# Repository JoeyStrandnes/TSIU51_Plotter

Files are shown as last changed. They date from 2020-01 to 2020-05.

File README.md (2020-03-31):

# Skittle Sort



Skittle sort är en sorteringsmaskin för kursen "Mikrodatorprojektet".

- 2x Servomotorer
- 2x ATMega16A
- 3D printad trumma 
- jm162a 2x16 numerisk LCD
- TCS34725 (RGB sensor)

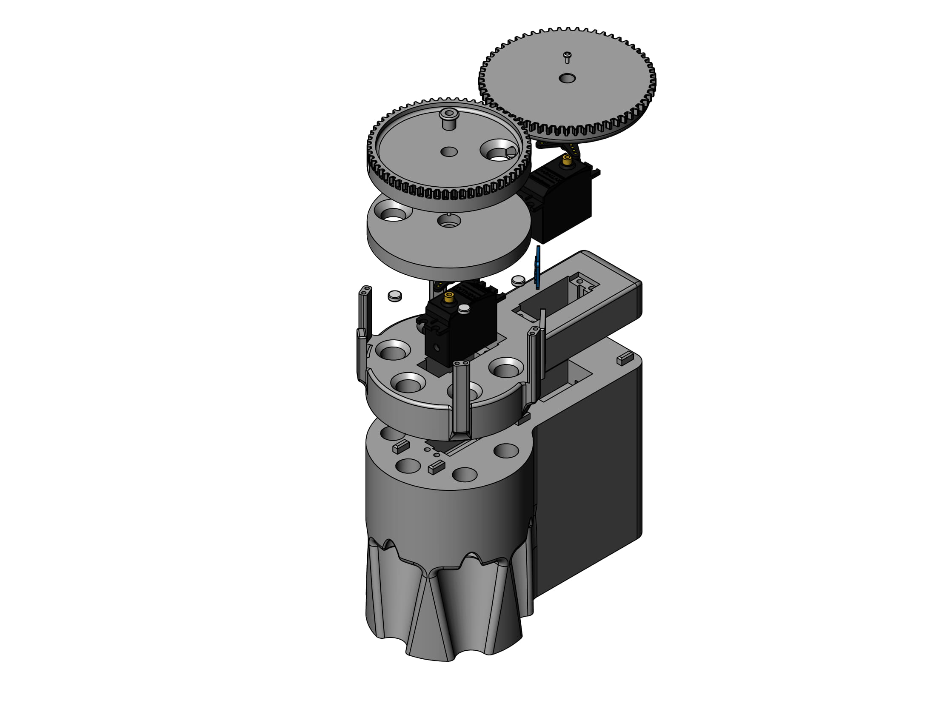
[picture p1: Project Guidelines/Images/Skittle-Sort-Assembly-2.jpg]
Assembly


PCB
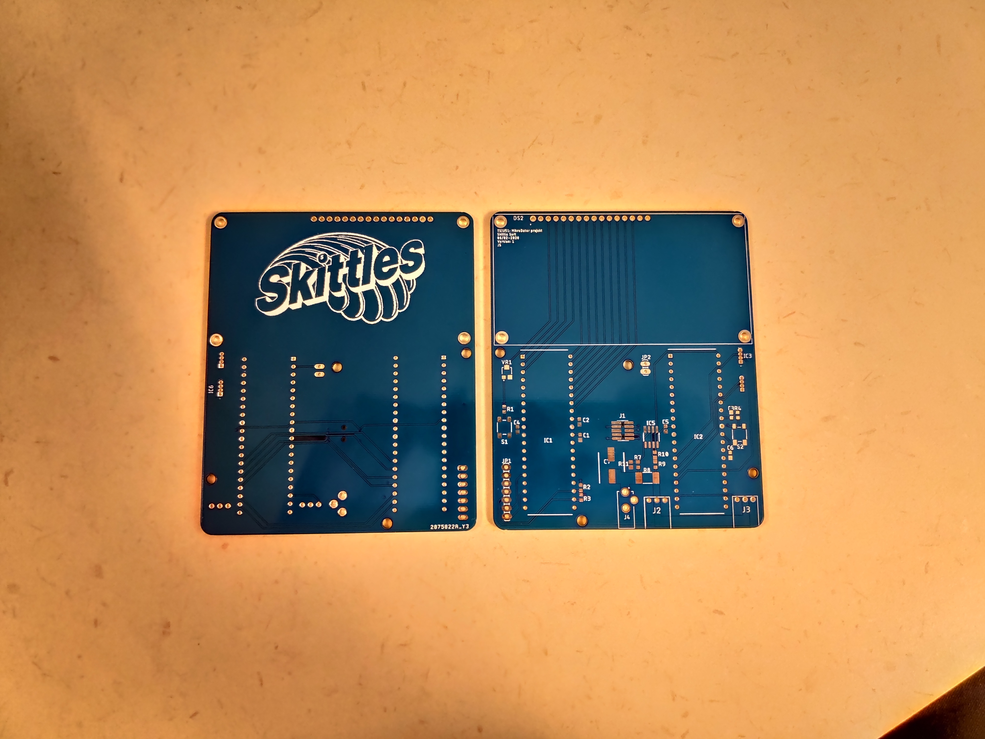
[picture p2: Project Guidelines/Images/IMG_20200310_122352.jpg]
PCB


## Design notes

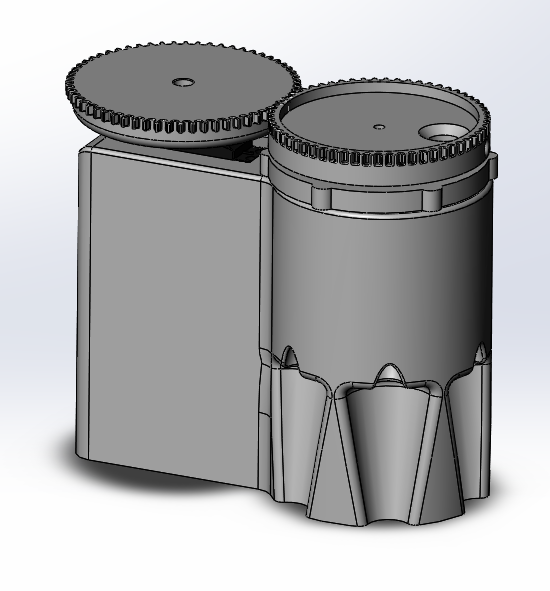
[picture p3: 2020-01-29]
Mechanical/Images/More Complete-2.png

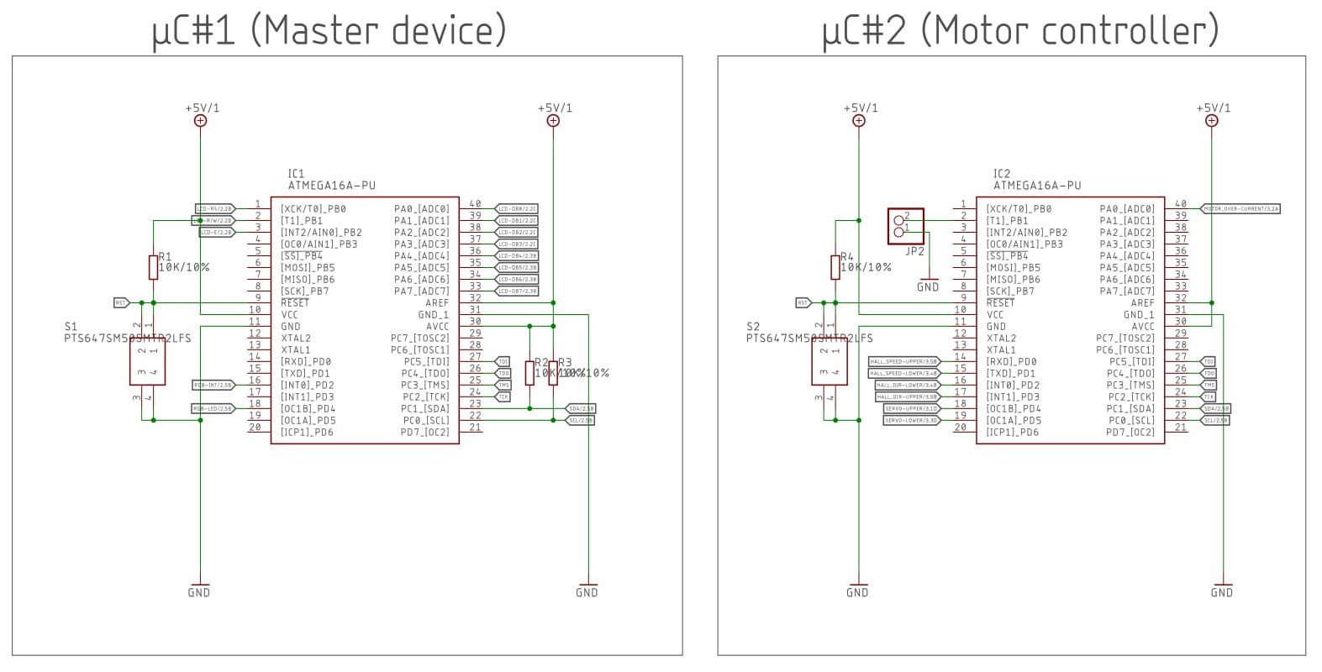
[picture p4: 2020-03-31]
Project Guidelines/Images/Schematic/Microcontroller.jpg

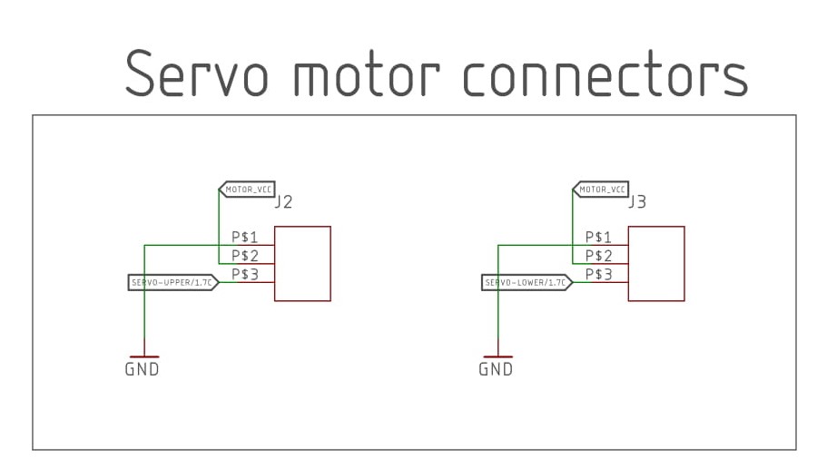
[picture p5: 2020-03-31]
Project Guidelines/Images/Schematic/Servo.jpg

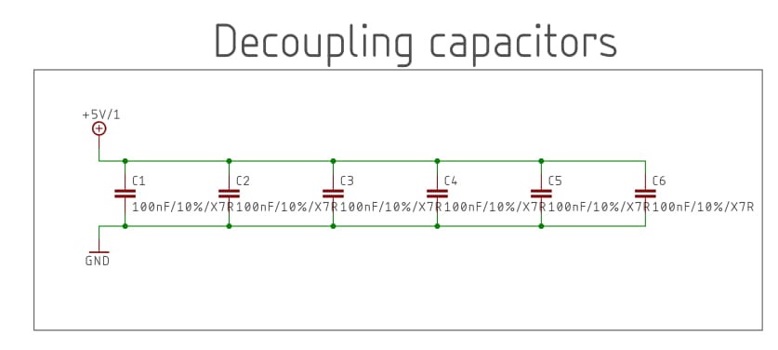
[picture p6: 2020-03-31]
Project Guidelines/Images/Schematic/Decoupling.jpg

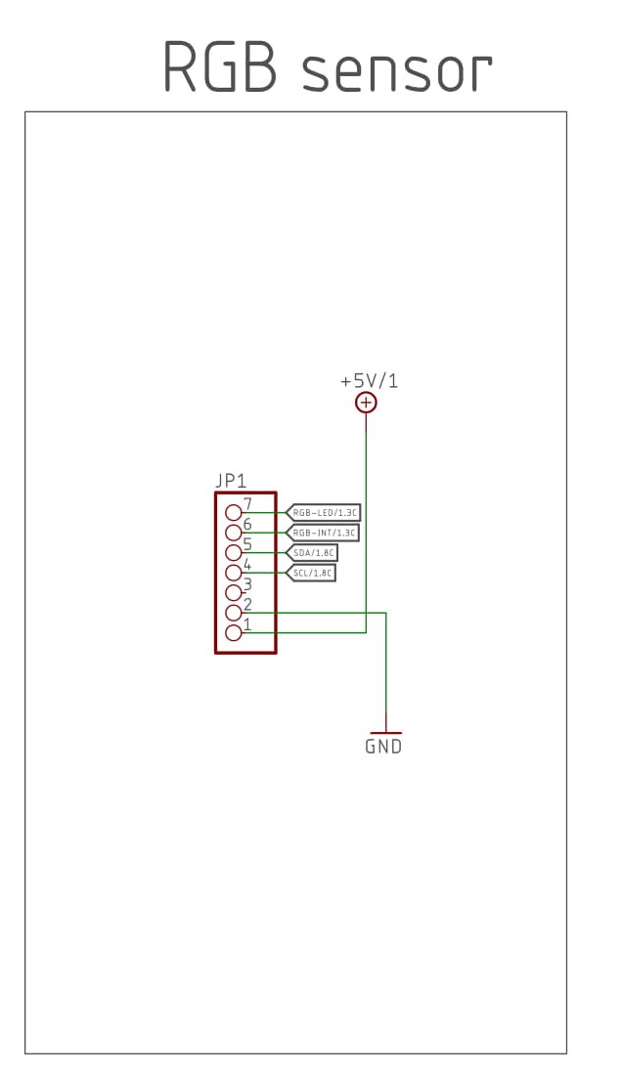
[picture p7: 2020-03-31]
Project Guidelines/Images/Schematic/RGB.jpg

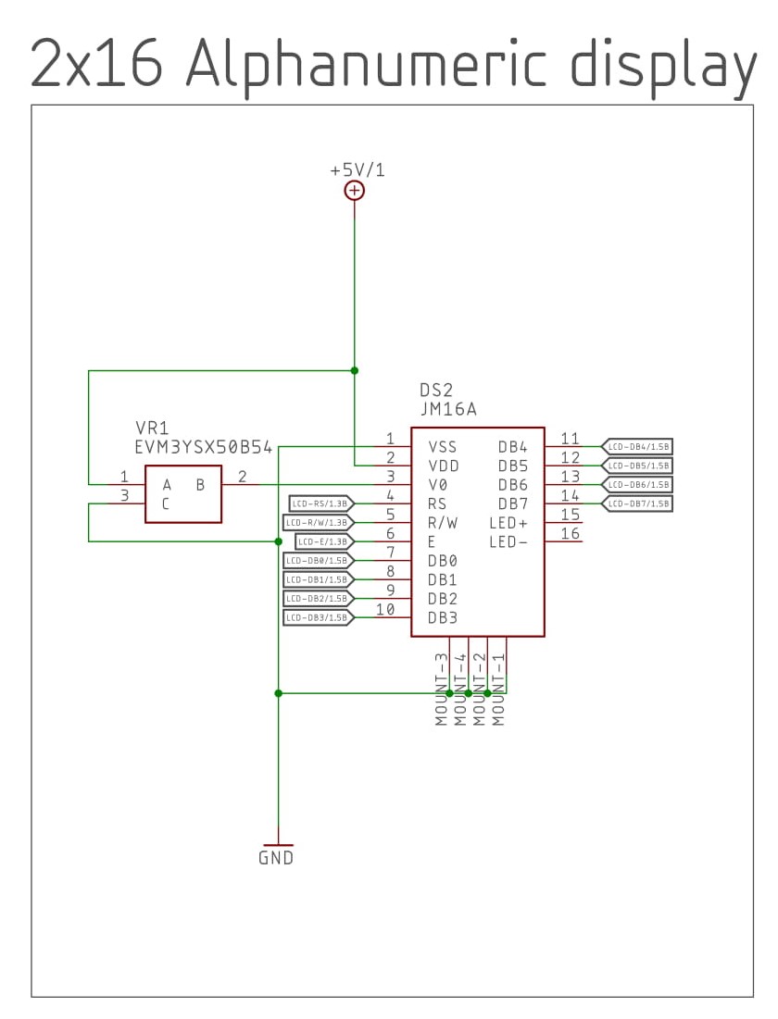
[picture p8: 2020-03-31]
Project Guidelines/Images/Schematic/LCD.jpg

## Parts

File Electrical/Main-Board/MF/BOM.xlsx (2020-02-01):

Qty | Value | Device | Package | Description | Purchase Link
2 | 22288033 | 22288033 | 22288033 | Pin header | https://se.rs-online.com/web/p/pcb-headers/1790561/
5 | 1.2K/5% | R-EU_R0603 | R0603 | RESISTOR, European symbol | https://se.rs-online.com/web/p/surface-mount-fixed-resistors/6621026/
6 | 100nF/10%/X7R | C-EUC0603 | C0603 | CAPACITOR, European symbol | https://se.rs-online.com/web/p/mlccs-multilayer-ceramic-capacitors/9040240/
6 | 10K/10% | R-EU_R0603 | R0603 | RESISTOR, European symbol | https://se.rs-online.com/web/p/surface-mount-fixed-resistors/8626704/
1 | 200R/5% | R-EU_R0603 | R0603 | RESISTOR, European symbol | https://se.rs-online.com/web/p/surface-mount-fixed-resistors/6789960/
2 | 500R/5% | R-EU_R0603 | R0603 | RESISTOR, European symbol | https://se.rs-online.com/web/p/surface-mount-fixed-resistors/1228894/
1 | 866R/5% | R-EU_R0603 | R0603 | RESISTOR, European symbol | https://se.rs-online.com/web/p/surface-mount-fixed-resistors/1229654/
2 | ATMEGA16A-PU | ATMEGA16A-PU | DIP1556W56P254L5232H483Q40N | ATMEGA16A-PU, 8 bit AVR Microcontroller 16MHz 16 kB, OBS: INGET MÅSTE, DRAR BARA NER STORLEKEN | https://se.rs-online.com/web/p/microcontrollers/1278276/
1 | AZ1117CH-5.0TRG1DITR-ND | AZ1117CH-5.0TRG1DITR-ND | SOT230P700X180-4N | LOW DROPOUT LINEAR REGULATOR | https://se.rs-online.com/web/p/low-dropout-voltage-regulators/9210688/
1 | AZ1117CH-ADJTRG1 | AZ1117CH-ADJTRG1 | SOT230P700X170-4N | 1.35A Adj. LDO Reg. Current Limit SOT223 DiodesZetex | https://se.rs-online.com/web/p/low-dropout-voltage-regulators/8287602/
1 | EEEFK1J220P | EEEFK1J220P | CAPAE800X650N | Panasonic Aluminium Electrolytic Capacitor 22uF 63V | https://se.rs-online.com/web/p/aluminium-capacitors/7083598/
1 | ERJ-L1WKF10CU | ERJ-L1WKF10CU | RESC6332X120N | RESISTOR, 2512 100 mOhm +/-1% 1W | https://se.rs-online.com/web/p/surface-mount-fixed-resistors/0566989/
1 | EVM3YSX50B54 | EVM3YSX50B54 | EVM3YSX50B54 | SMD Cermet Trimmer Pot, 3mm Sq, 50K | https://se.rs-online.com/web/p/trimmer-resistors/7312880/
1 | FTSH-105-01-L-DV-K-A-P-TR | FTSH-105-01-L-DV-K-A-P-TR | FTSH10501LDVKAPTR | Samtec FTSH, 1.27mm Pitch, 10 Way, 2 Row PCB Termina | https://se.rs-online.com/web/p/pcb-headers/0451732/
1 | LM2904DRG3 | LM2904DRG3 | SOIC127P600X175-8N | Dual general-purpose operational amplifier (Finns ej på RS, nästa bästa) | https://se.rs-online.com/web/p/op-amps/1449253/
1 | NHD-0216XZ-FSW-GBW | NHD-0216XZ-FSW-GBW | NHD0216XZFSWGBW | LCD Character Display Modules & Accessories STN- GRA | -
1 | PJ-031DH | PJ-031DH | PJ031DH | DC Power Connectors Power Jacks (Finns ej på RS, nästa bästa) | https://se.rs-online.com/web/p/dc-power-sockets/1224871/
2 | PTS647SM50SMTR2LFS | PTS647SM50SMTR2LFS | PTS647SM50SMTR2LFS | Tactile Switches 50mA 12VDC, 1.8N 5.0mm H, G leads (Finns ej på RS, nästa bästa) | https://se.rs-online.com/web/p/tactile-switches/0255667/
5 | TLE4966L | TLE4966L | TLE4966L | Infineon TLE4966L, Bipolar Hall Effect Sensor Switch | https://se.rs-online.com/web/p/hall-effect-sensor-ics/1107464/
2 | Servo Motor |  |  |  | https://se.rs-online.com/web/p/servo-motors/7813046/

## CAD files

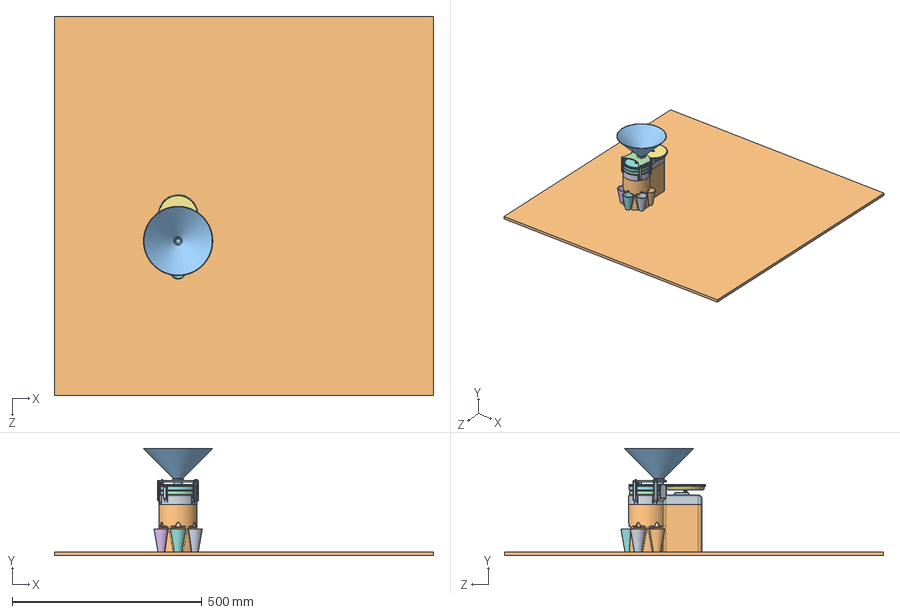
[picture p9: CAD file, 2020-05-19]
Mechanical/Skittle-Sort-Assembly.SLDASM
1000.0 x 283.4 x 1000.0 mm
Slide-Top
User Library-Futaba-Parallax-ContinuousRatationServo x 2
Lower-Disk
User Library-Futaba-Servo-X-Horn x 2
2mm-Screw x 2
Upper-Servo-Gear
Upper-Disk-ALT
Shaft-Spacer
Slide-Bottom
tcs34725
Upper-Shaft-Retainer
Magnet-8mm x 5
Glass-R
Glass-G
Glass-Y
Glass-O
Glass-P
M3x16mm x 2
Transistor_TO-92_Type

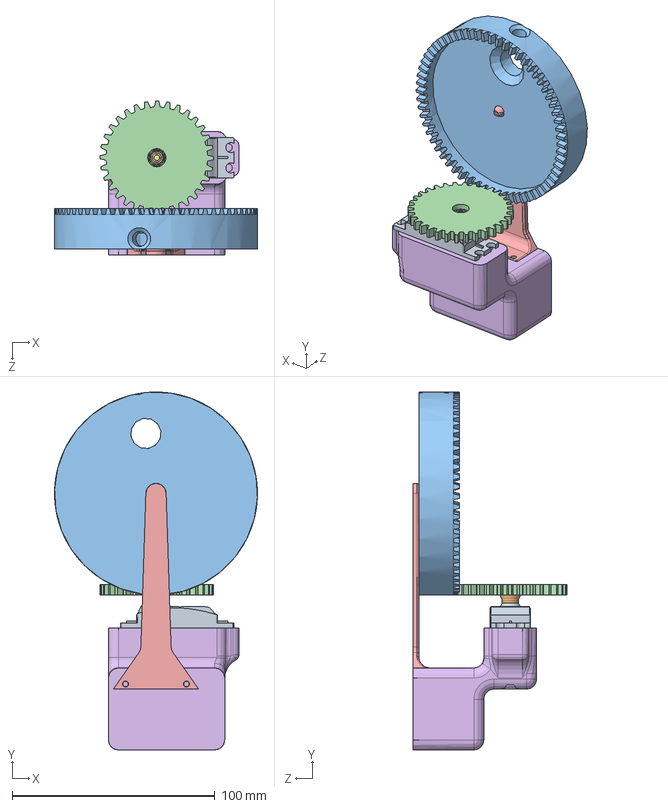
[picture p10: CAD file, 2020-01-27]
Mechanical/Top-Sorter-SubAssembly.SLDASM
100.0 x 176.4 x 76.0 mm
User Library-Futaba-Parallax-ContinuousRatationServo
User Library-Futaba-Servo-X-Horn
Upper-Disk
Upper-Servo-Gear
Top-Holder
Top-Motor-Holder
2mm-Screw

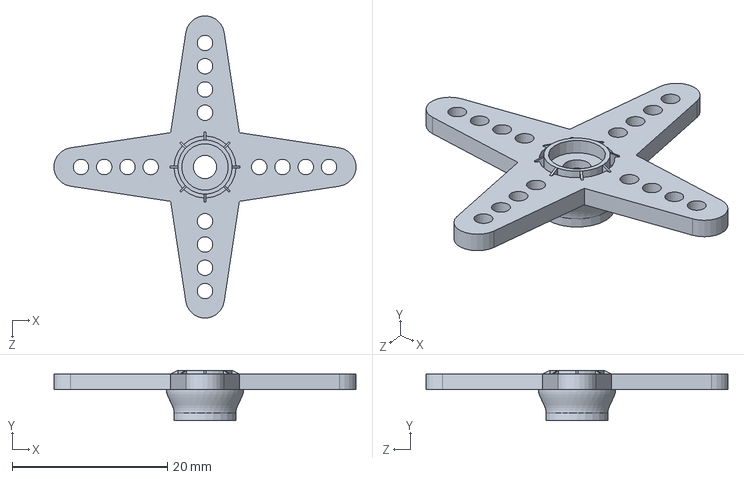
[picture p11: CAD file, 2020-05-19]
Mechanical/Servo From manufacturer/User Library-Futaba-Servo-X-Horn.sldprt
39.0 x 6.50 x 39.0 mm

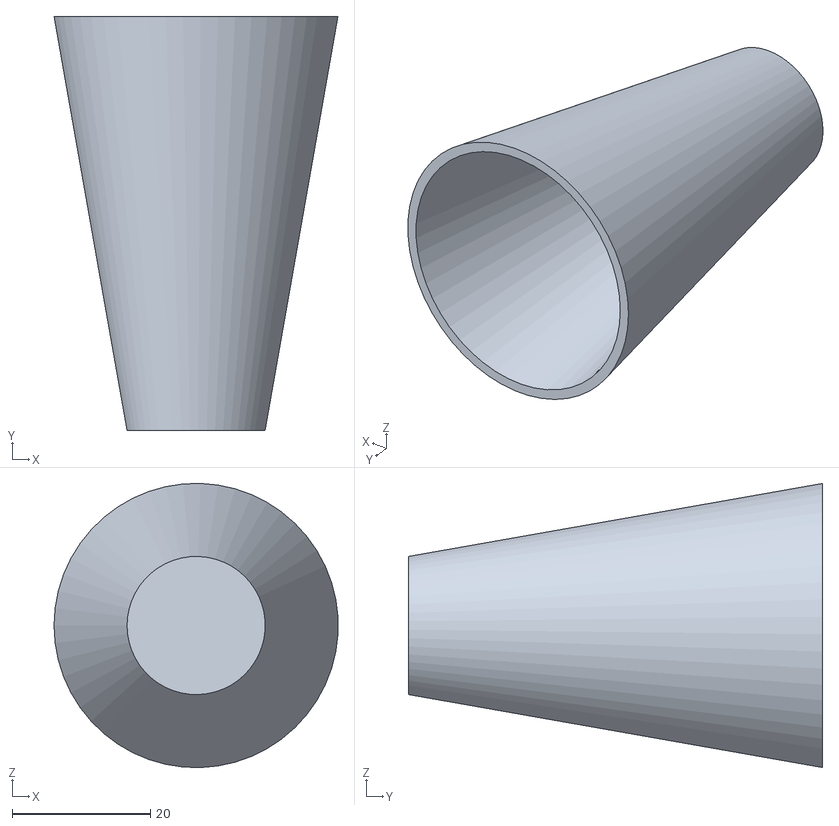
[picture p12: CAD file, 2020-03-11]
Mechanical/STL Files/Cup.STL
41.1 x 60.0 x 41.1

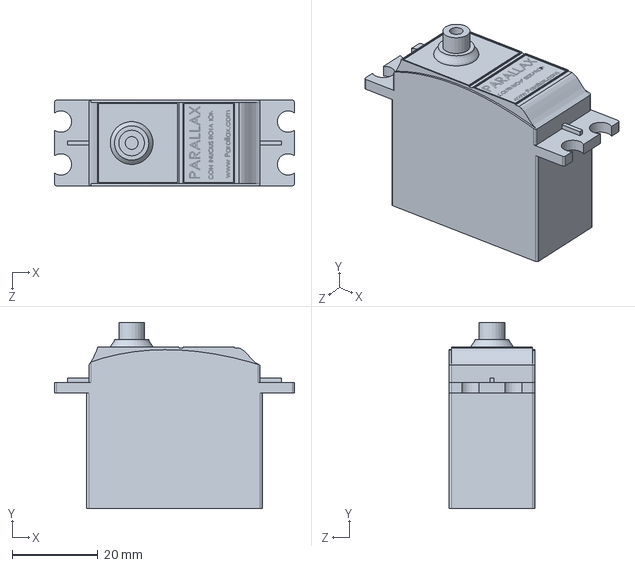
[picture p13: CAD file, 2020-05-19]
Mechanical/Servo From manufacturer/User Library-Futaba-Parallax-ContinuousRatationServo.sldprt
56.0 x 43.5 x 20.0 mm

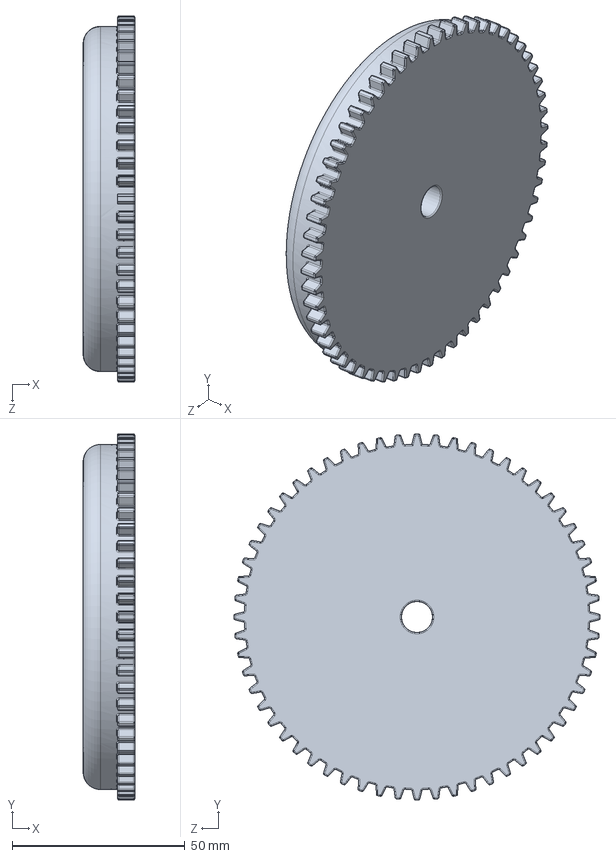
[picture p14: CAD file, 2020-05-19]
Mechanical/Upper-Servo-Gear.SLDPRT
15.0 x 106.0 x 106.0 mm

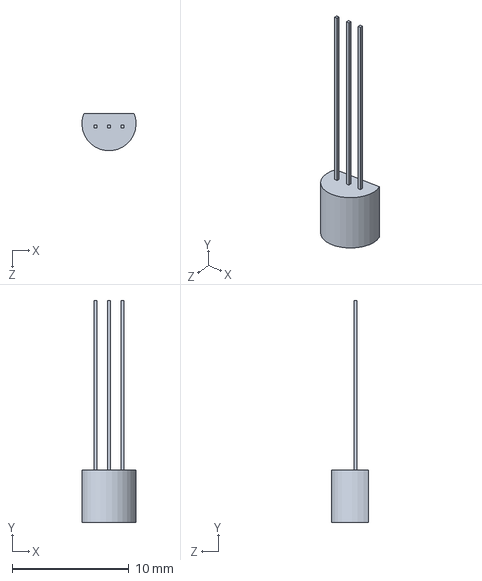
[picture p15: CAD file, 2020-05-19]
Mechanical/Transistor_TO-92_Type.SLDPRT
4.64 x 19.0 x 3.19 mm

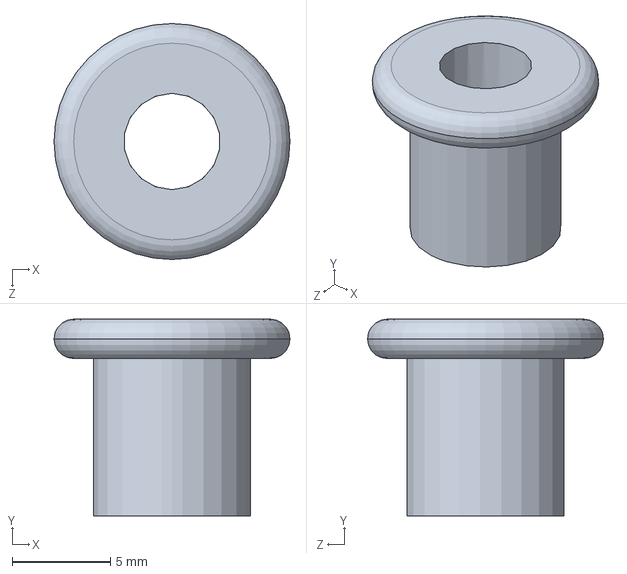
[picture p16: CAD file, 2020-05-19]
Mechanical/Upper-Shaft-Retainer.SLDPRT
12.0 x 10.0 x 12.0 mm

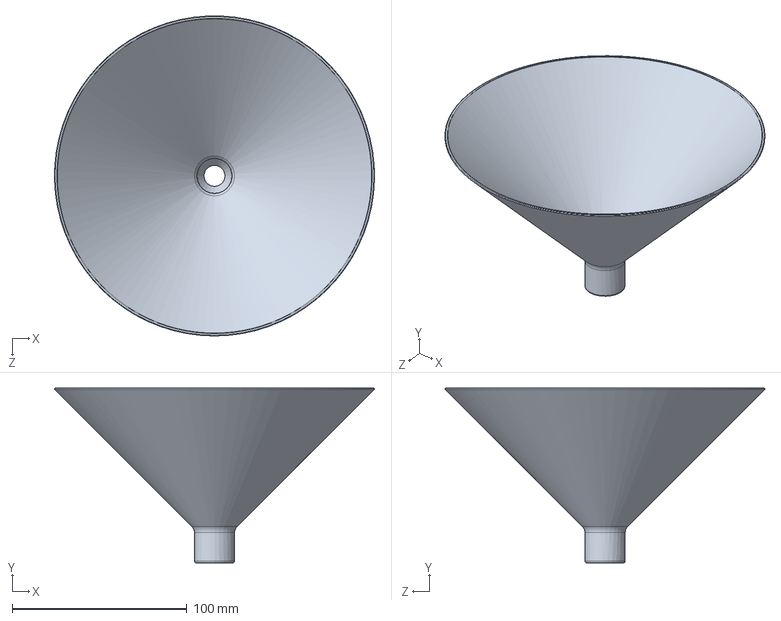
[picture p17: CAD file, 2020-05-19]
Mechanical/Funnel.SLDPRT
183.1 x 100.0 x 183.0 mm

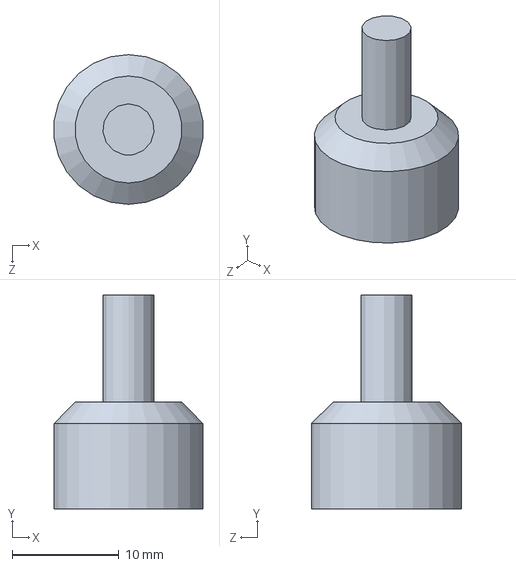
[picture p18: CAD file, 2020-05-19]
Mechanical/Shaft-Spacer.SLDPRT
13.9 x 20.0 x 14.0 mm

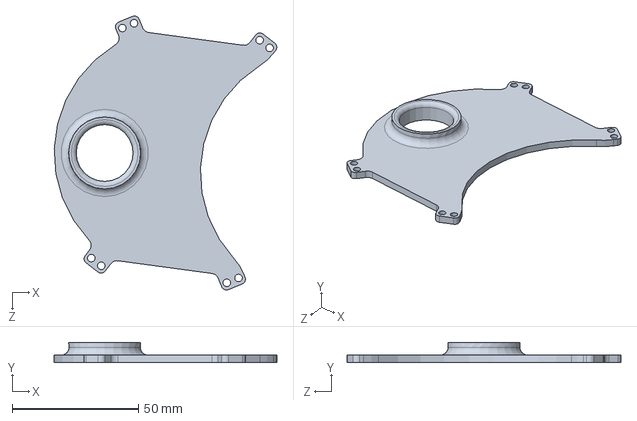
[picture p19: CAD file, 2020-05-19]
Mechanical/Funnel Retainer.SLDPRT
88.1 x 8.00 x 108.5 mm

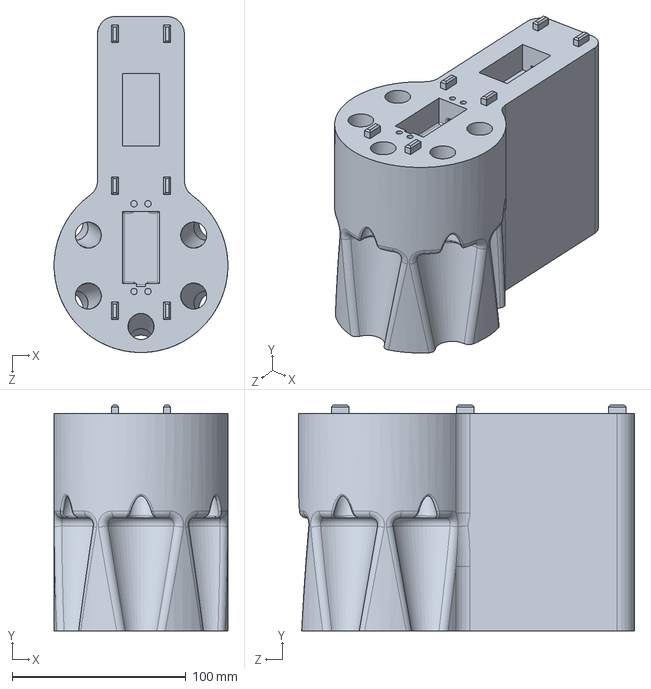
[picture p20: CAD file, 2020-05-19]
Mechanical/Slide-Bottom.SLDPRT
100.0 x 130.0 x 193.3 mm

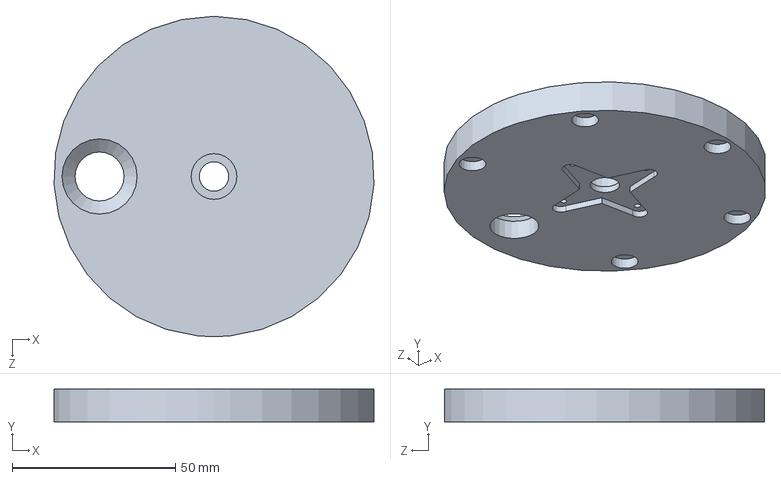
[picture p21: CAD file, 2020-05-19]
Mechanical/Lower-Disk.SLDPRT
97.9 x 10.0 x 98.0 mm

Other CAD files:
Mechanical/Glass-G.SLDPRT
Mechanical/Glass-P.SLDPRT
Mechanical/Glass-R.SLDPRT
Mechanical/Glass-O.SLDPRT
Mechanical/Glass-Y.SLDPRT
Mechanical/2mm-Screw.SLDPRT
Mechanical/Drawings/Disk-Draw.SLDDRW
Mechanical/Floor.SLDPRT
Mechanical/Glass.SLDPRT
Mechanical/M3x16mm.SLDPRT
Mechanical/Magnet-8mm.SLDPRT
Mechanical/Parallax-900-000XX_ServoMotor.SLDPRT
Mechanical/STL Files/Funnel Retainer.STL
Mechanical/STL Files/Funnel.STL
Mechanical/STL Files/Lower-Disk.STL
Mechanical/STL Files/Slide-Bottom.STL
Mechanical/STL Files/Slide-Top.STL
Mechanical/STL Files/Upper-Shaft-Retainer.STL
Mechanical/Skittle.SLDPRT
Mechanical/Slide-BACKUP.SLDPRT
Mechanical/Slide-Top.SLDPRT
Mechanical/Top-Holder.SLDPRT
Mechanical/Top-Motor-Holder.SLDPRT
Mechanical/Upper-Disk-ALT.SLDPRT
Mechanical/Upper-Disk-Retainer.SLDPRT
Mechanical/Upper-Disk.SLDPRT
Mechanical/tcs34725.sldprt

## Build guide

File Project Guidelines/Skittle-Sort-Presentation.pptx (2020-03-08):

## Skittle Sort

Mikrodatorprojekt - TSIU51

## Krav & Mål

- Sortera Skittles beroende på färg
- Visa data på LCD
- Kommunicera över I2C

## Funktionsdiagram

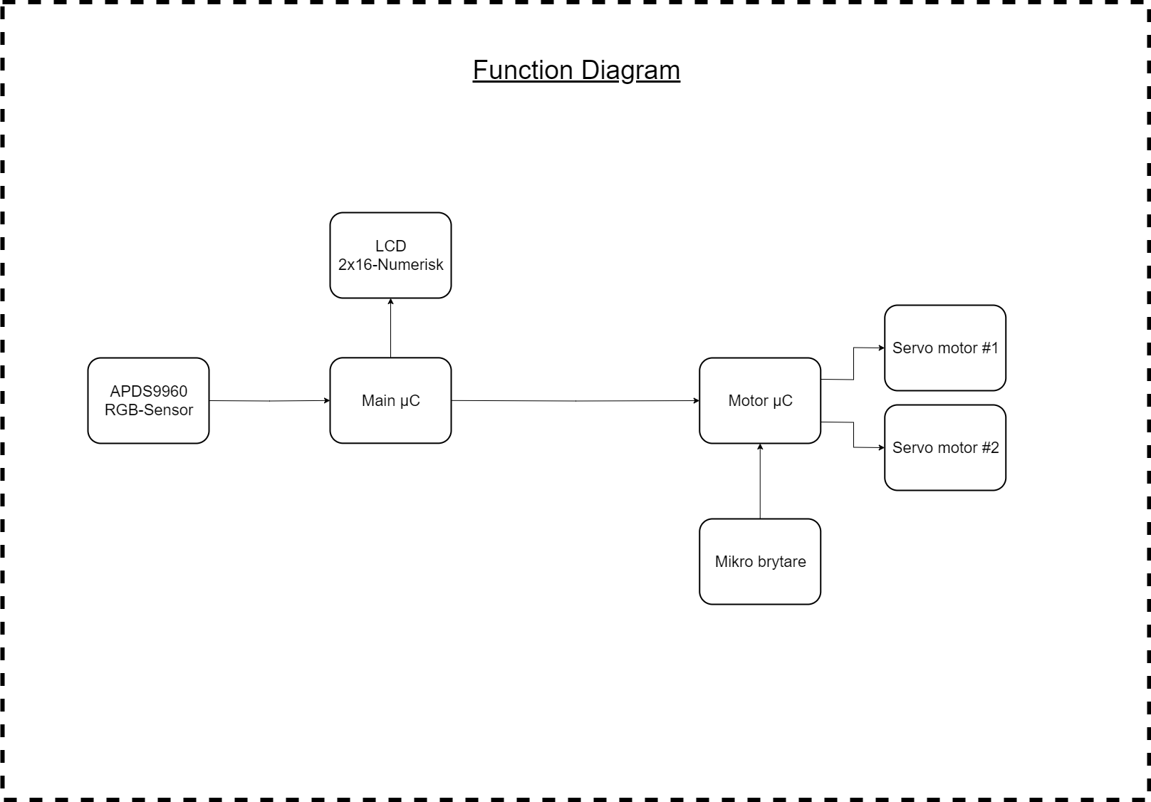
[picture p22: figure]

## Elektronik

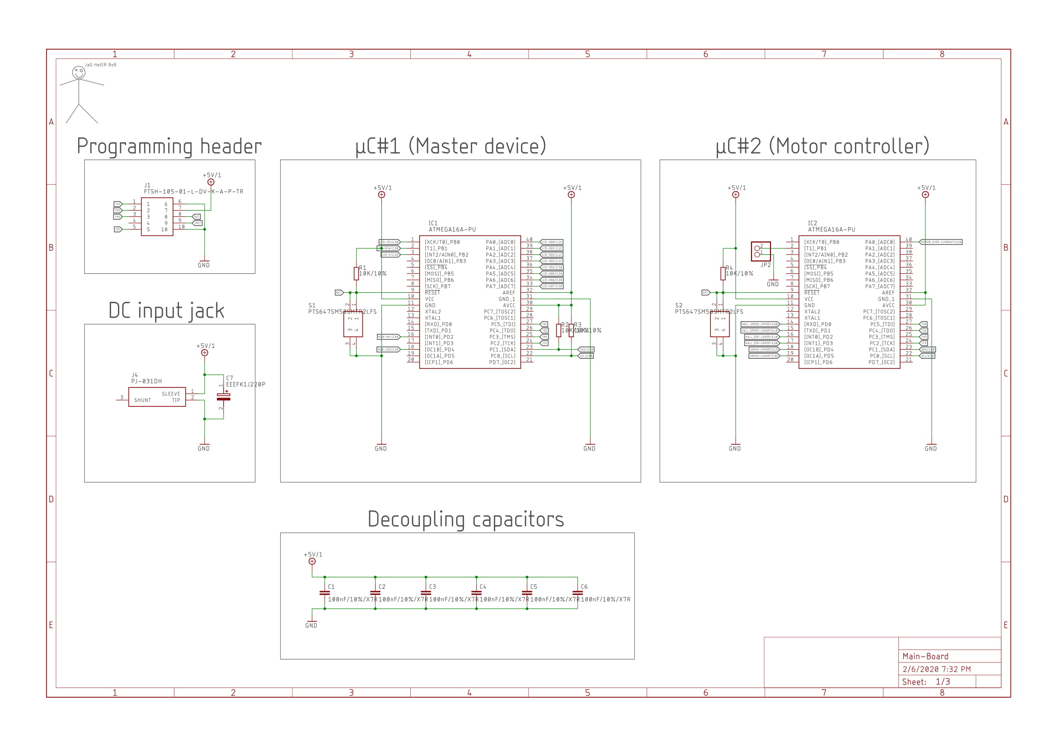
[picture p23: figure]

JM16A (LCD)
TCS34725 (RGB sensor)
LM2904DRG3
2x ATMega16A
2x A1120/22
2x Parallax 900-00008

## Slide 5

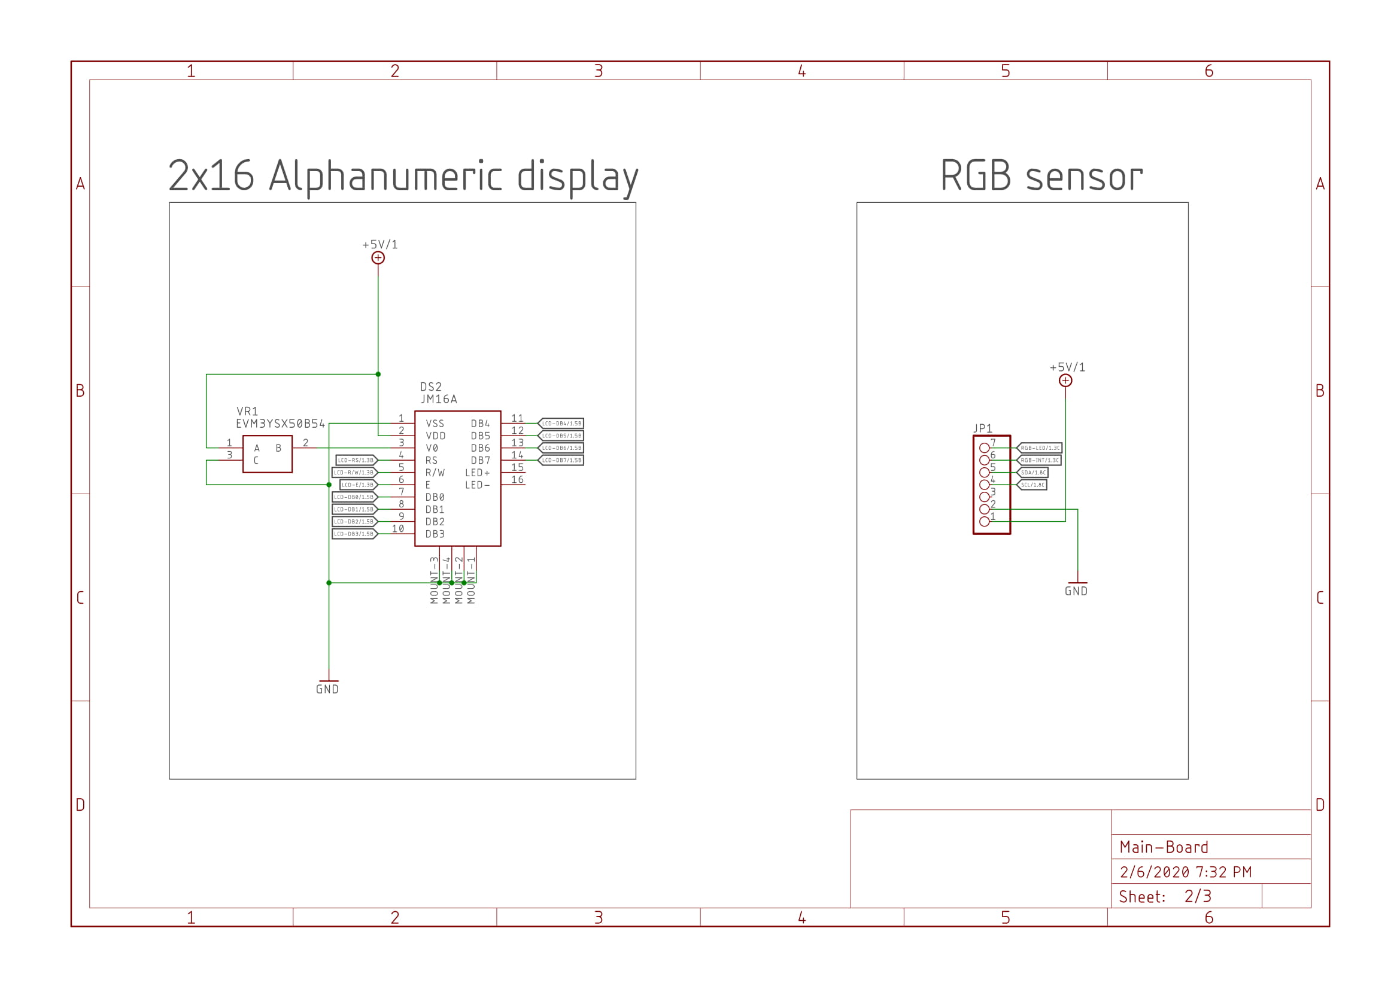
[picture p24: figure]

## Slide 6

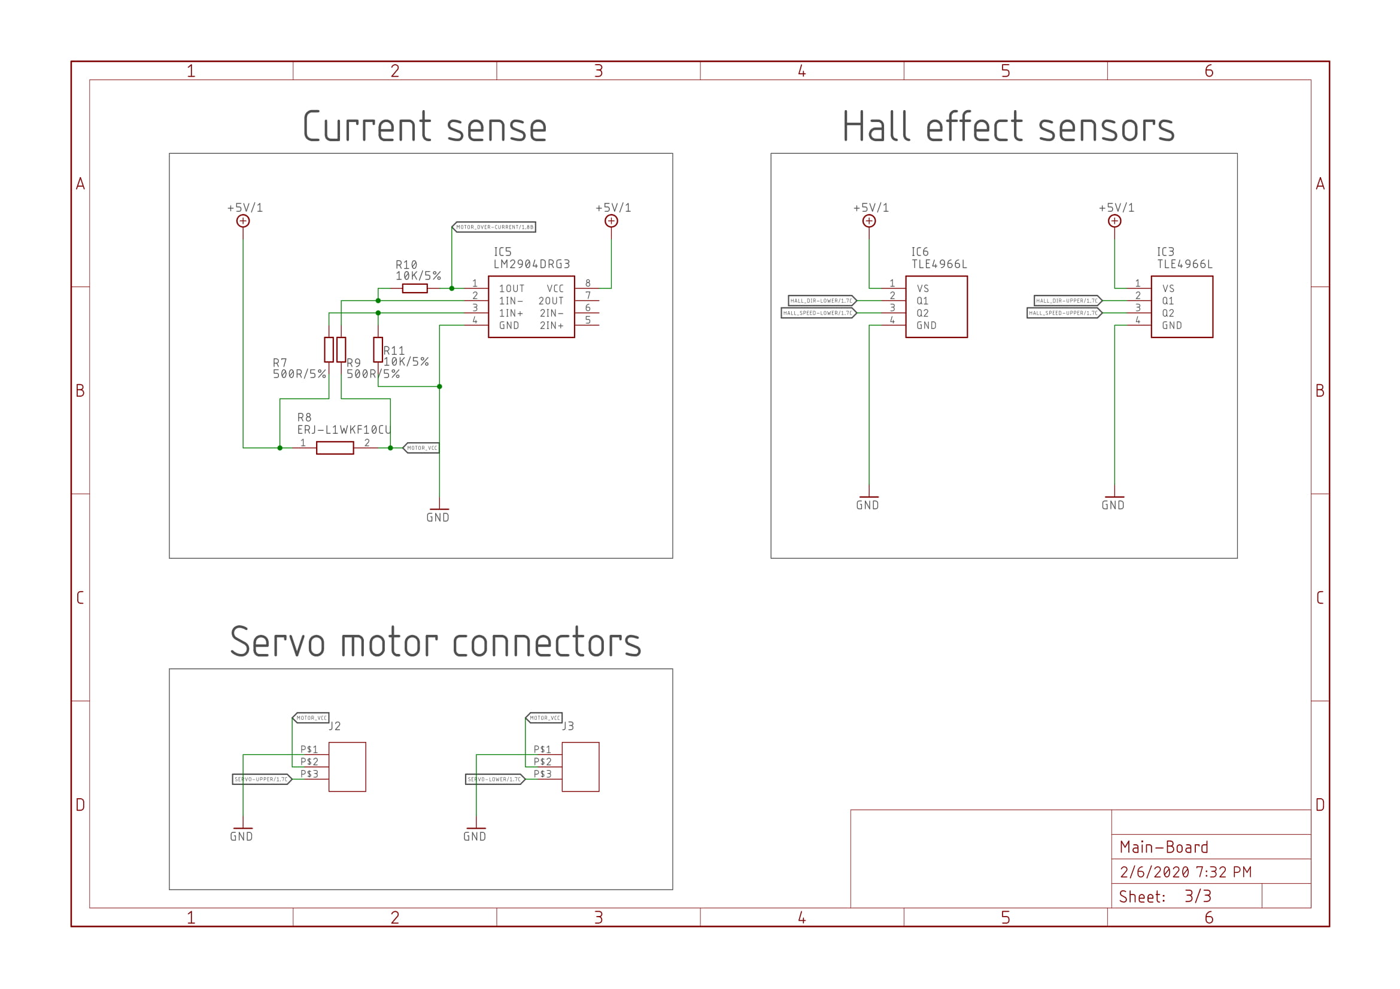
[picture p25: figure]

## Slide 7

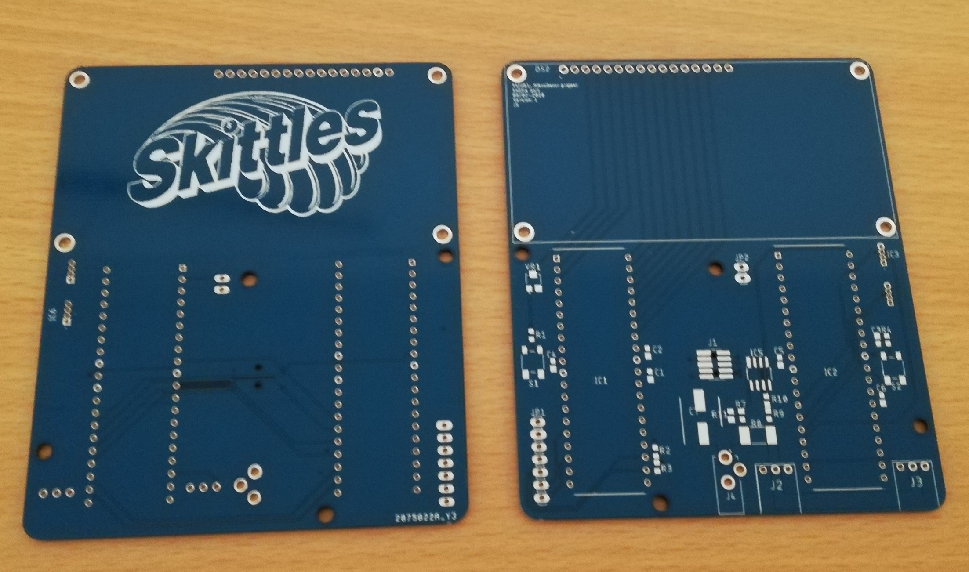
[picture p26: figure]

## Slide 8

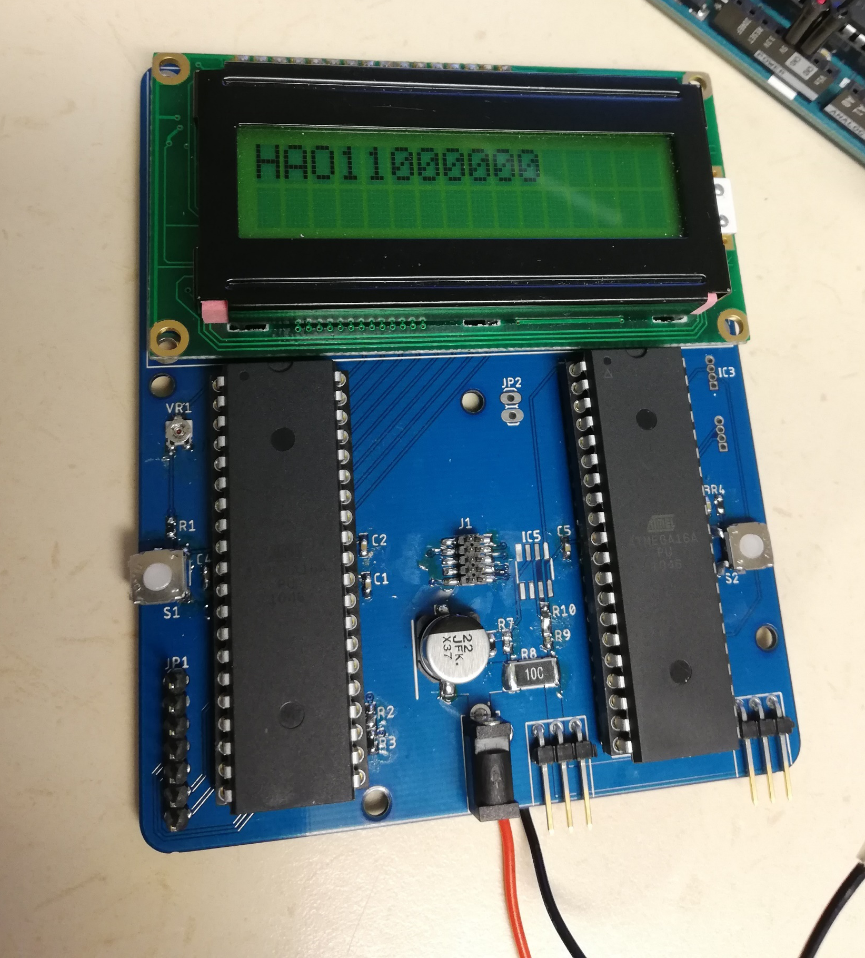
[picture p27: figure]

## Mekanik

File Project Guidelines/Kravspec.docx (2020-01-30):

TSIU51 – Skittle Sort

Kravspecifikation

Skittle sort är en sorteringsmaskin för Skittle’s. Maskinen är en egenkonstruerad mekanisk lösning som använder 2st ”Paralax: 900-00025” servomotorer för den mekaniska sortering. ”RGB-sensorn -TCS34725” används för att differentiera de olika färgarna på godiset. Godiset ligger i en tratt.

Grundkrav:

- Microkontroller:1
  - Färgmätning, färgsensorn TCS34725 kommunicerar över I2C (som slav).
  - Skicka instruktioner till µC:2 över I2C (µC:1 konfigurerad som master).
  - Visa antal sorterade på LCD (2x16-Alfanumerisk).
- Microkontroller:2
  - Styra två stycken servomotorer för sorteringen.
  - Brytare för att positionera trumman till rätt utgångsläge.
  - Ta emot instruktioner från µC:1 över I2C (µC:2 konfigurerad som slav).

Utökade krav:

- Spela melodi när sorteringen är färdig.
- Spara totalt antal sorterade Skittles i EEPROM.

Preliminär skiss på sorteringsmekaniken

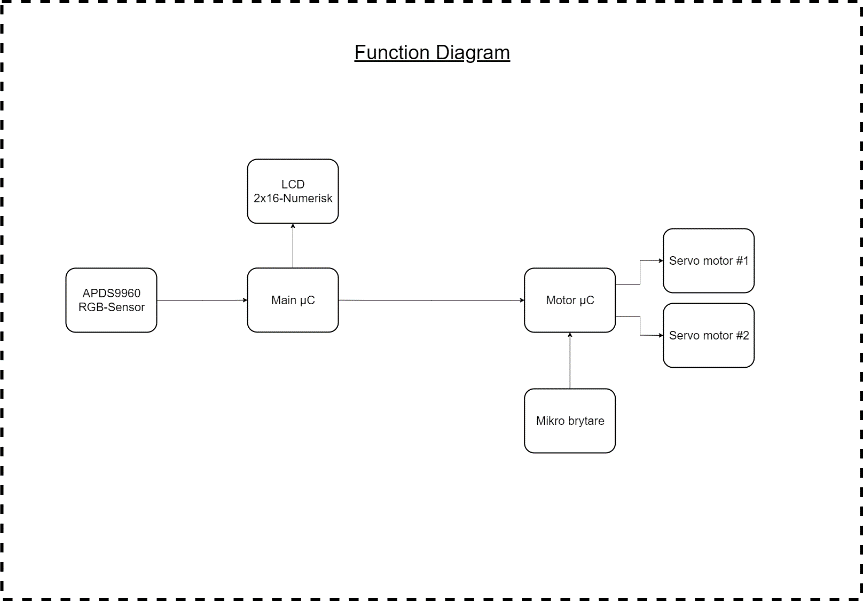
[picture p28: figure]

MPN | QTY | Description | Purchase link
900-00025 | 2 | SERVOMOTOR RC 180 RPM 6-8V | https://www.mouser.se/ProductDetail/Parallax/900-00025?qs=%2Fha2pyFaduiVyqoz07GqtC9sR9PU6dzGMTErRG1IkzY%3D
900-00008 | 2 | *ALTERNATIVT* | https://www.digikey.com/product-detail/en/parallax-inc/900-00008/900-00008-ND/1774454
AZ1117CH-ADJTRG1 | 2 | IC REG LIN POS ADJ 800MA SOT223 | https://www.digikey.com/product-detail/en/diodes-incorporated/AZ1117CH-ADJTRG1/AZ1117CH-ADJTRG1DICT-ND/4505208
AZ1117CH-5.0TRG1 | 1 | IC REG LINEAR 5V 800MA SOT223 | https://www.digikey.com/product-detail/en/diodes-incorporated/AZ1117CH-5.0TRG1/AZ1117CH-5.0TRG1DICT-ND/4505207
ESE-18R11B | 2 | SWITCH DETECTOR SPST-NO 10MA 5V | https://www.digikey.com/product-detail/en/panasonic-electronic-components/ESE-18R11B/P14175STR-ND/1972885
APDS9960 | 1 | RGB-sensor | -
LM2904DR | 2 | IC OPAMP GP 2 CIRCUIT 8SOIC | https://www.digikey.com/product-detail/en/texas-instruments/LM2904DR/296-14596-1-ND/555533
JM162A | 1 | Alphanumeric LCD | -
Skittles | 2 | Skittles godis (Sorteras) | https://www.kolonialvaror.se/product/skittles-fruits-1x1600g-mars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

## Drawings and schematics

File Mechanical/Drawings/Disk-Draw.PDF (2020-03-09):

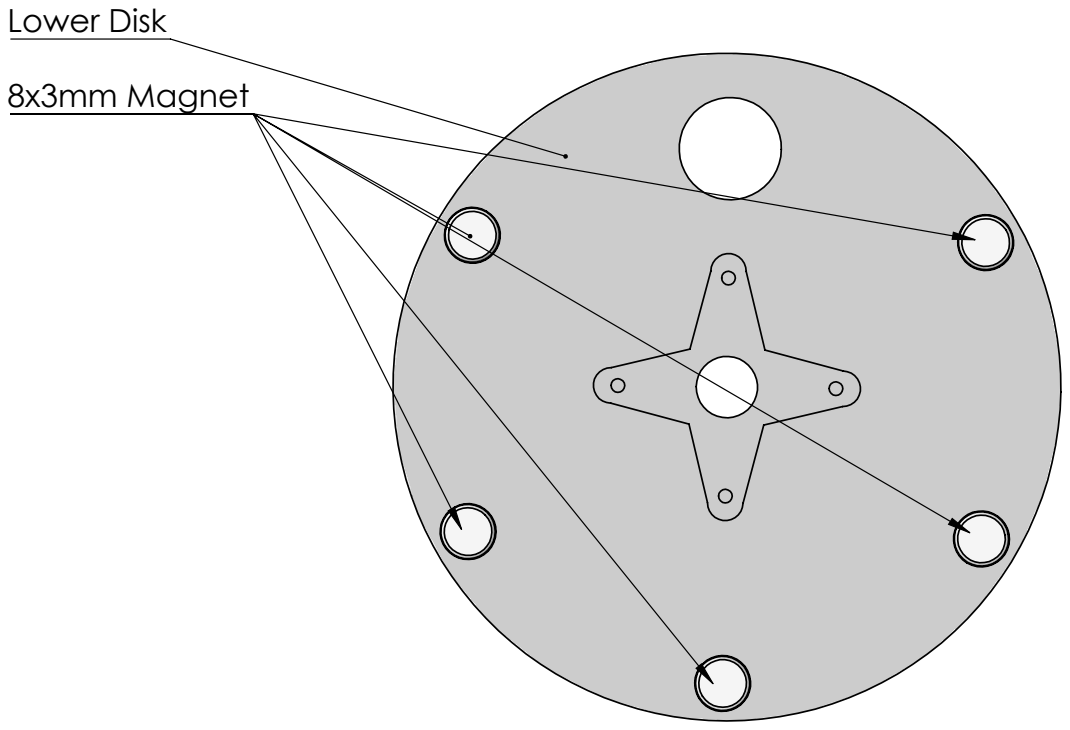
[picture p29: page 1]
8x3mm Magnet; Lower Disk

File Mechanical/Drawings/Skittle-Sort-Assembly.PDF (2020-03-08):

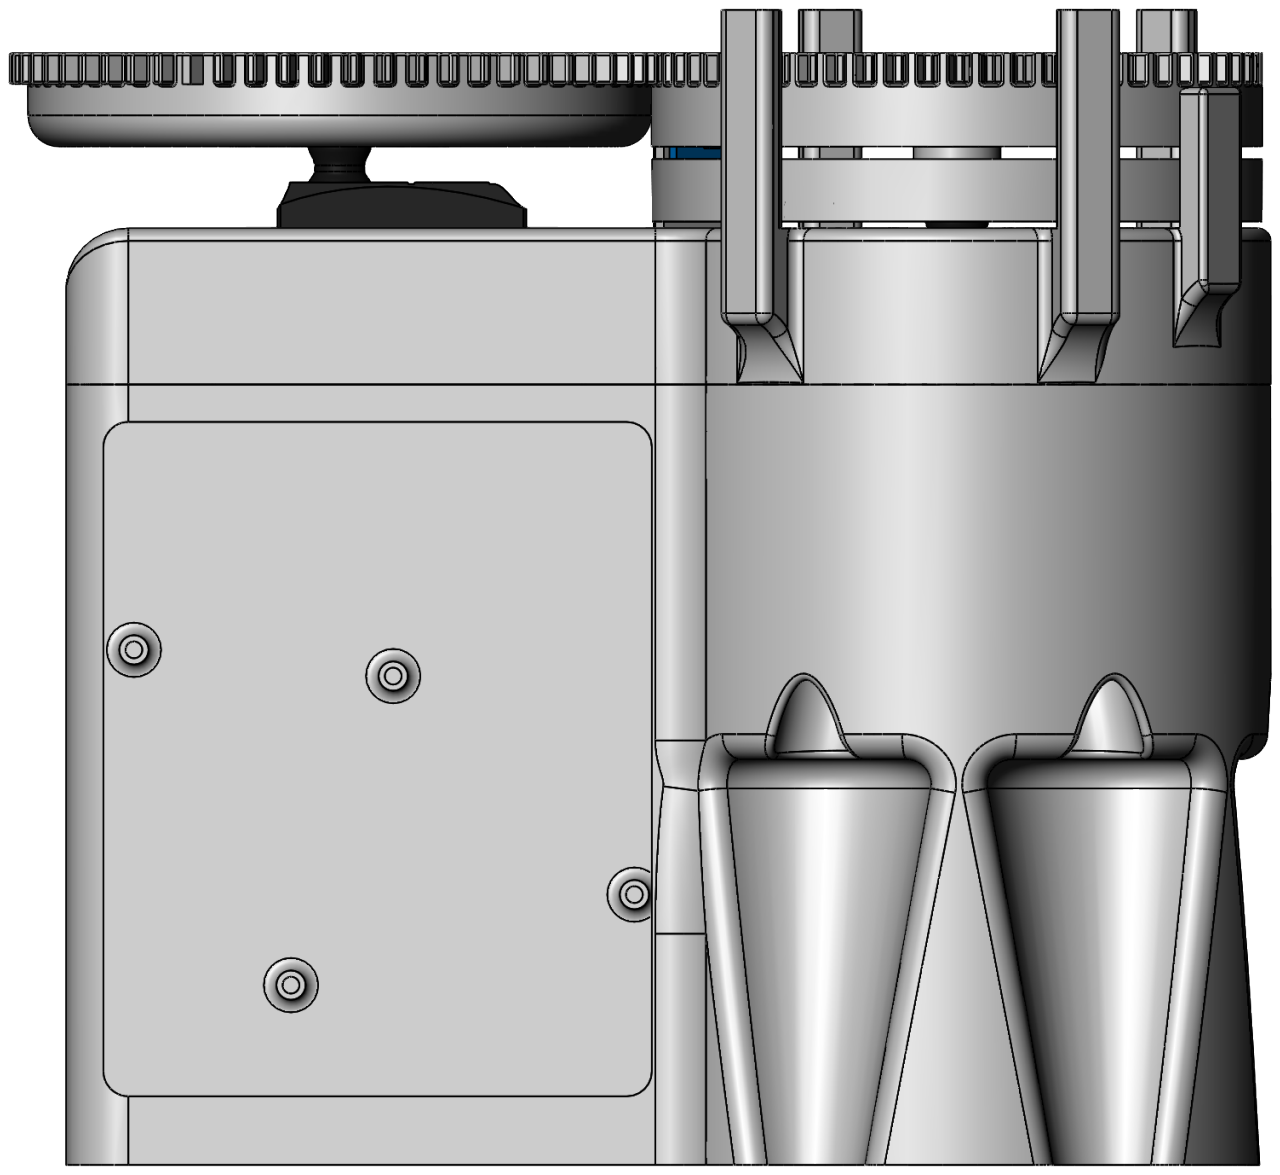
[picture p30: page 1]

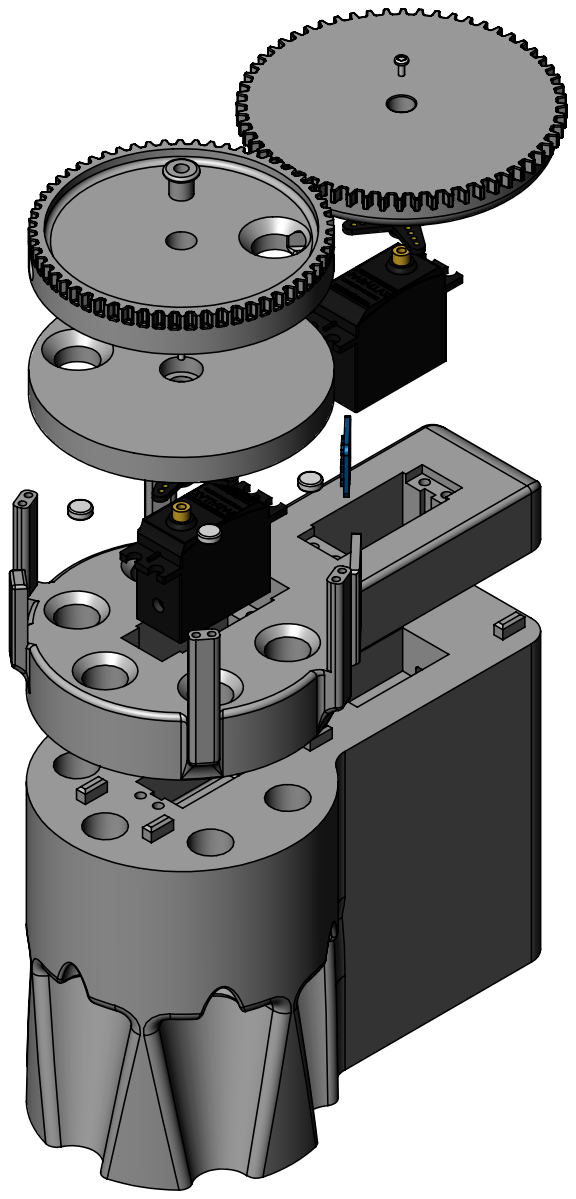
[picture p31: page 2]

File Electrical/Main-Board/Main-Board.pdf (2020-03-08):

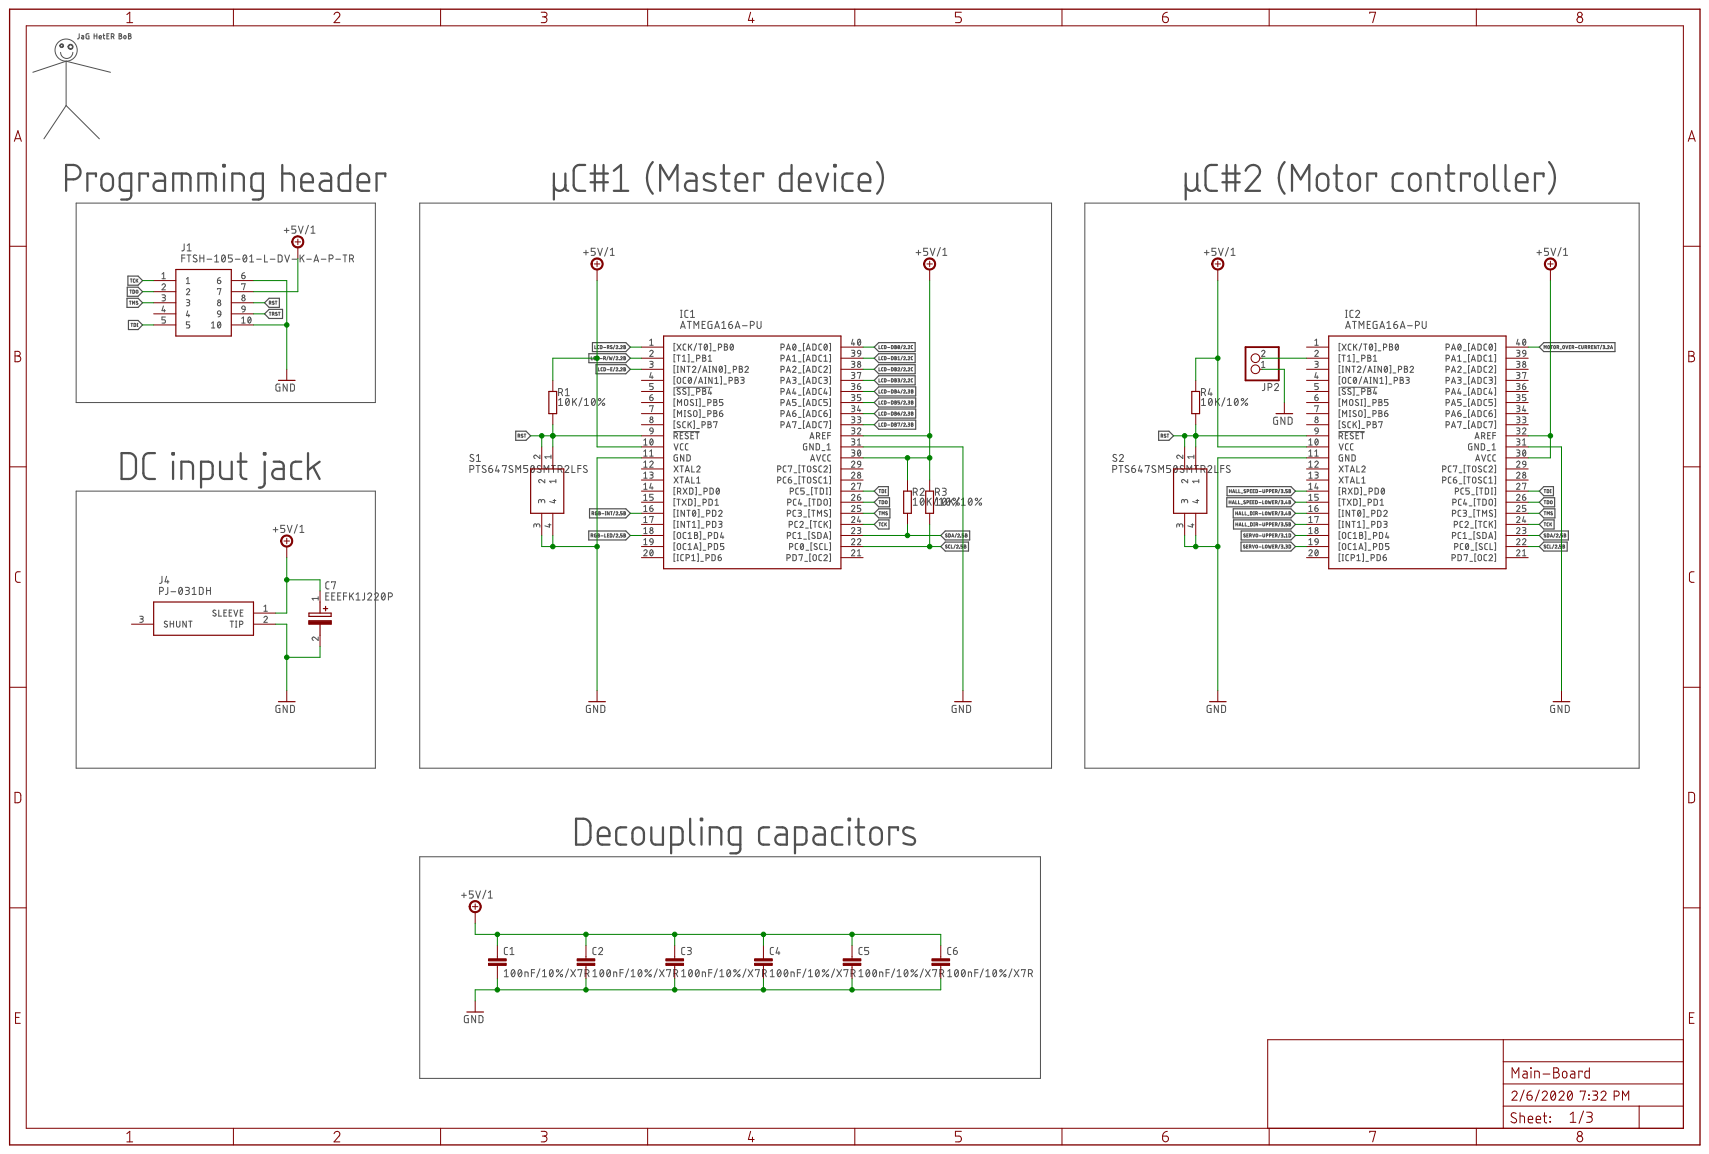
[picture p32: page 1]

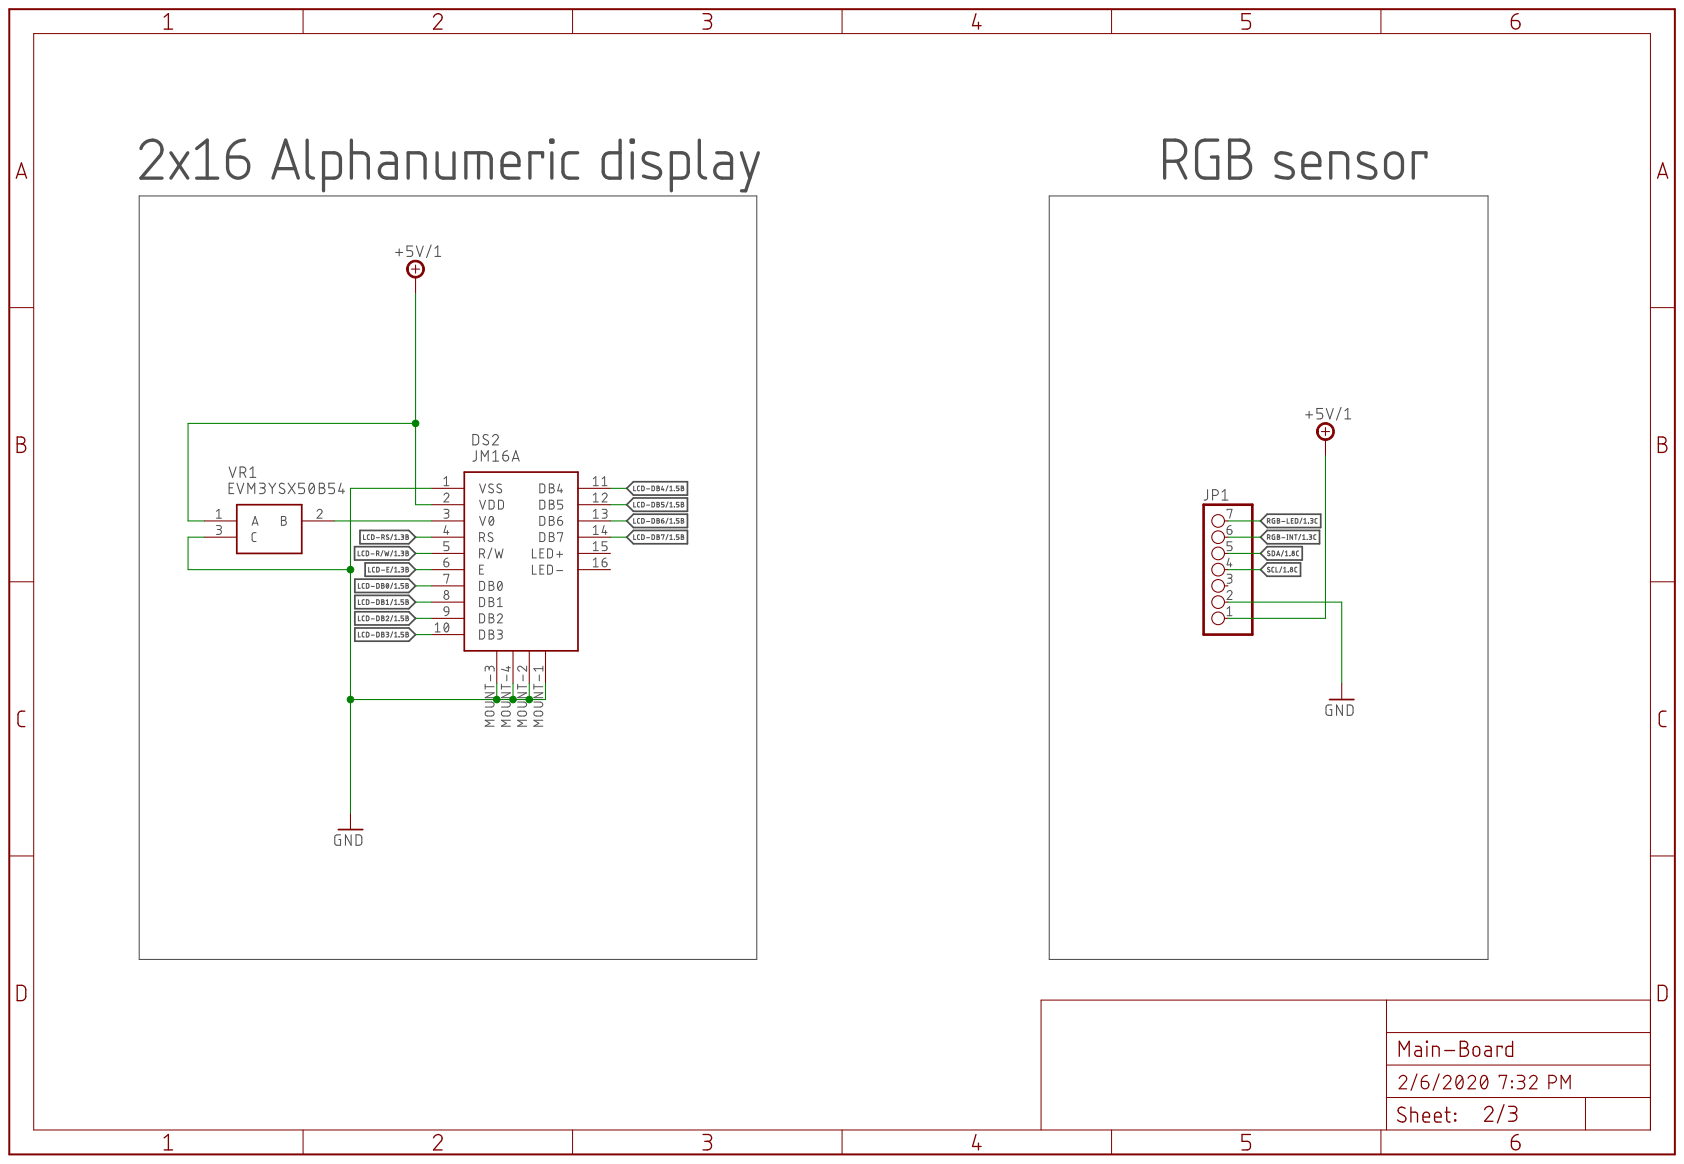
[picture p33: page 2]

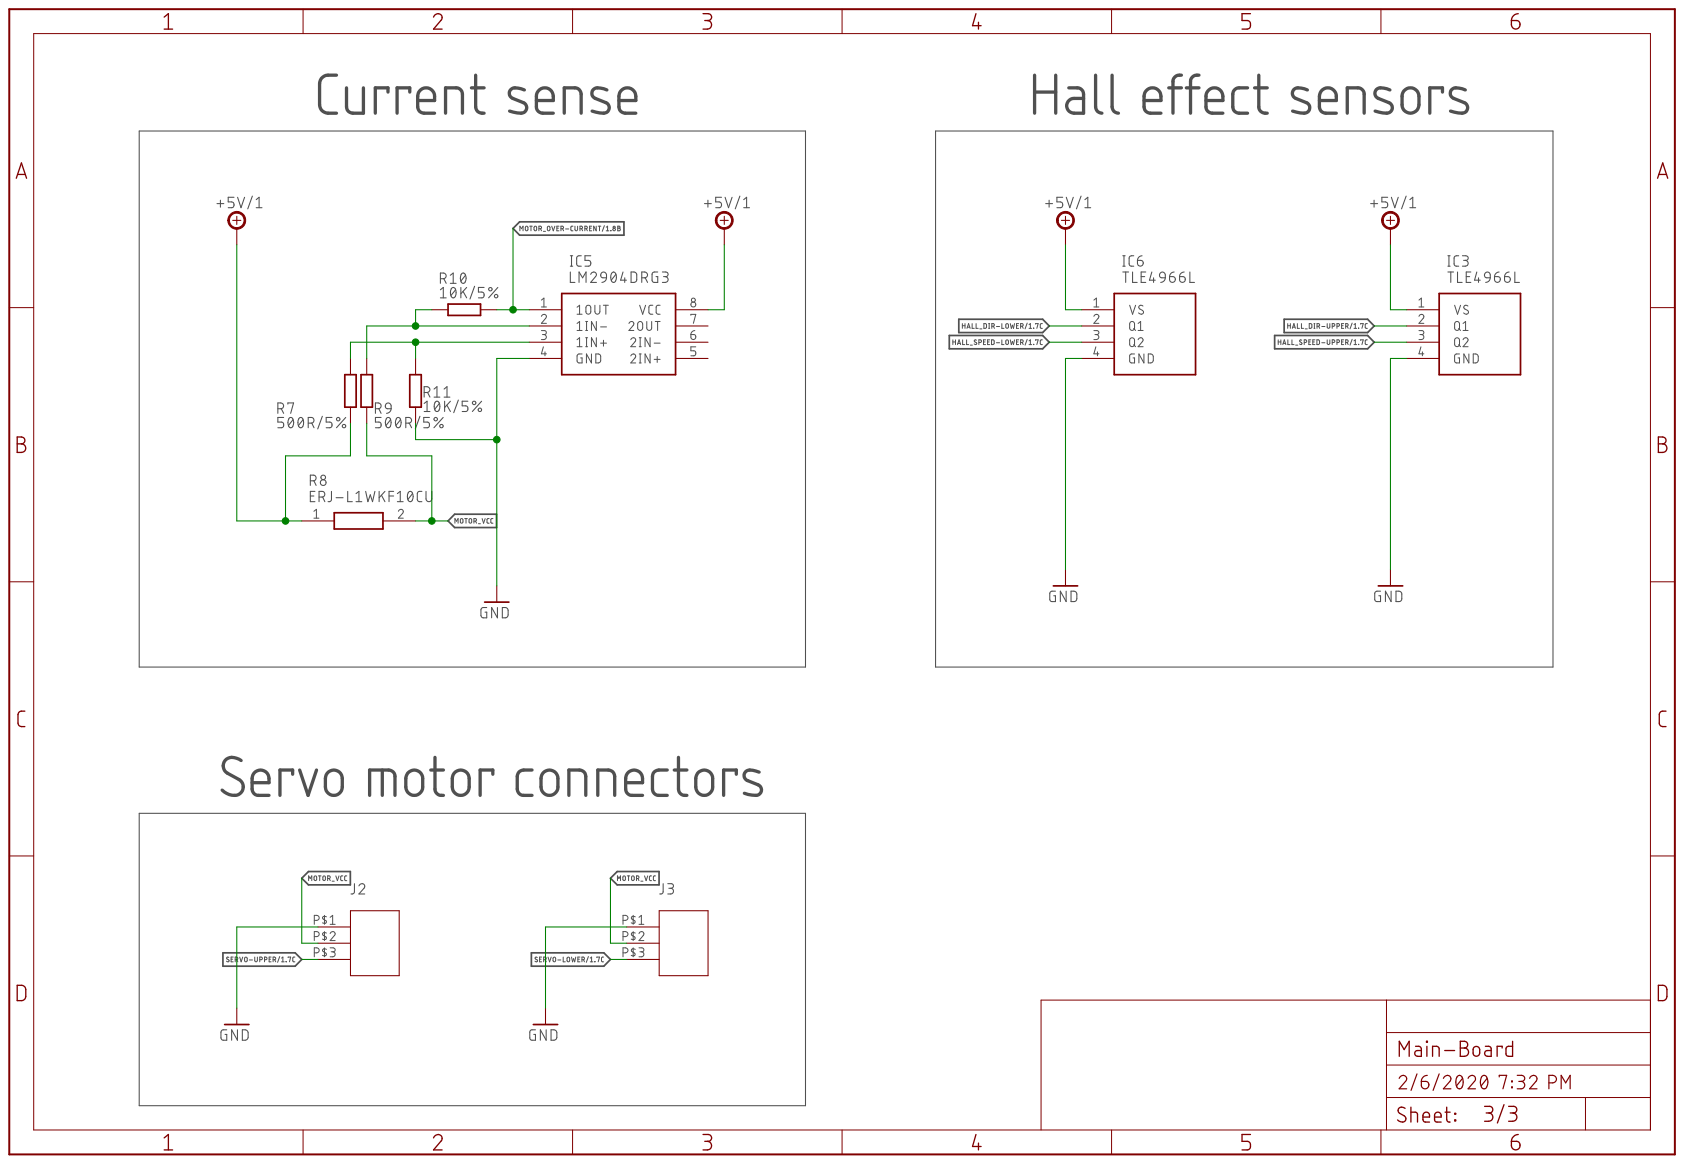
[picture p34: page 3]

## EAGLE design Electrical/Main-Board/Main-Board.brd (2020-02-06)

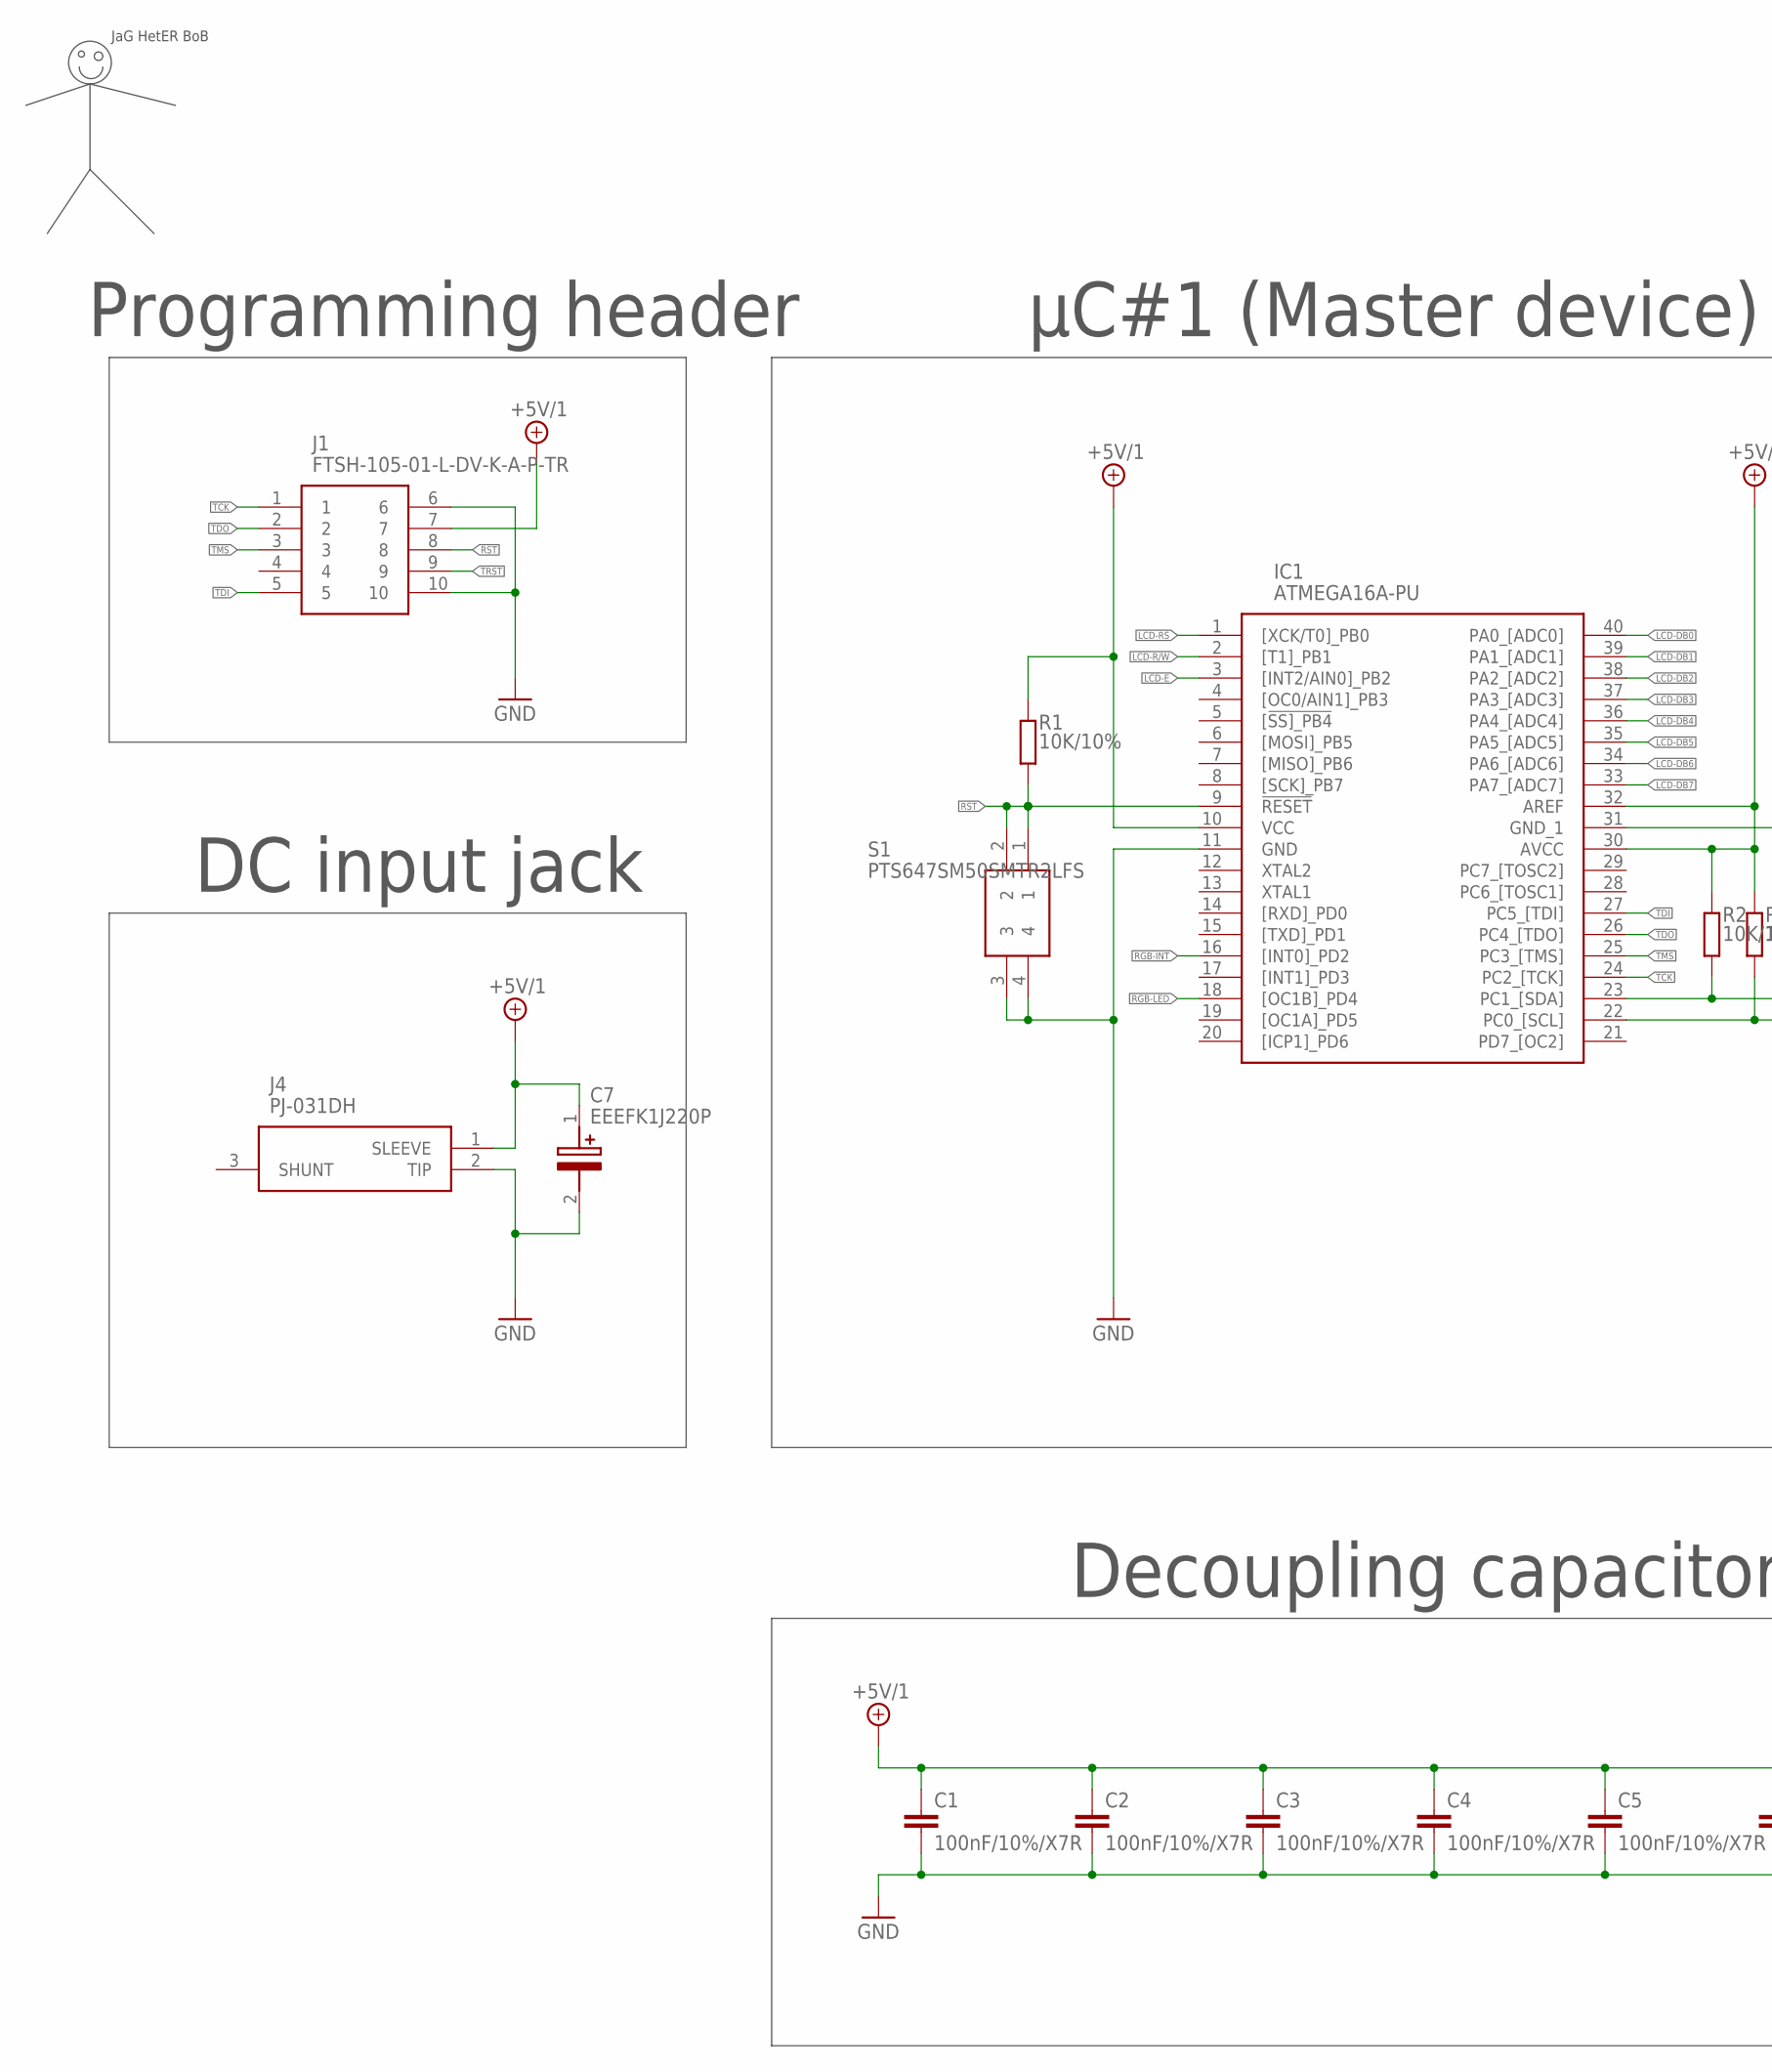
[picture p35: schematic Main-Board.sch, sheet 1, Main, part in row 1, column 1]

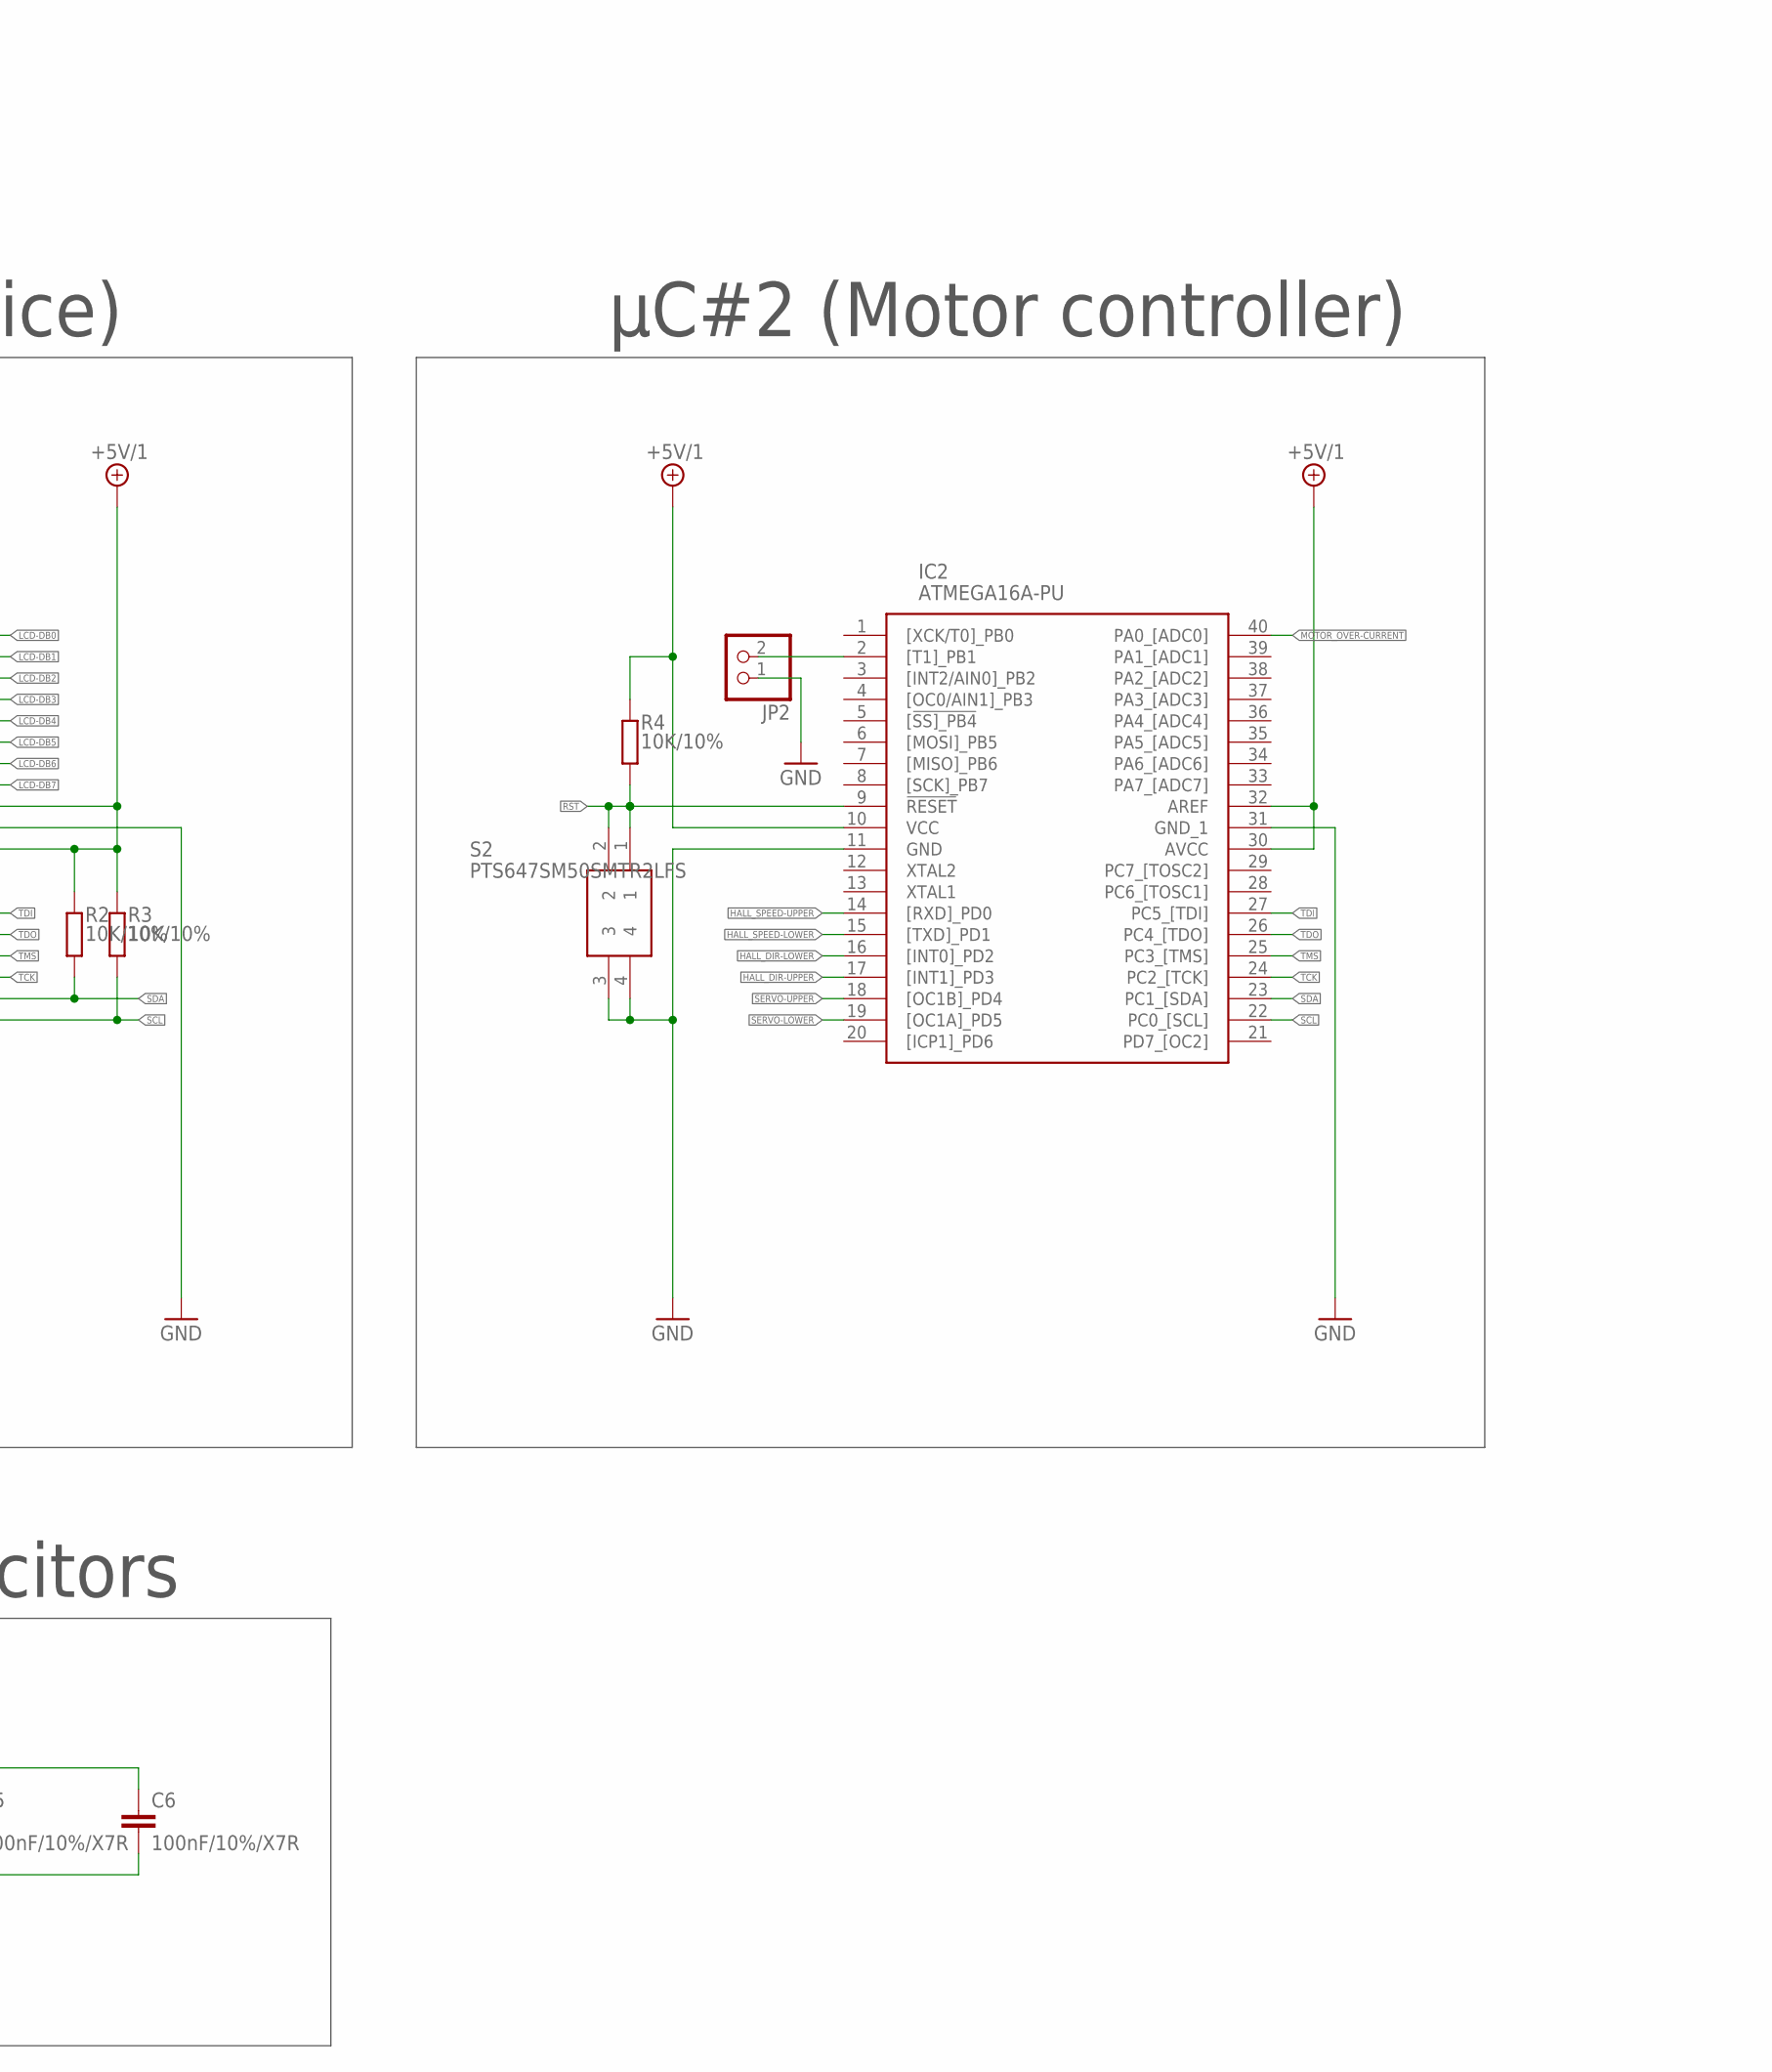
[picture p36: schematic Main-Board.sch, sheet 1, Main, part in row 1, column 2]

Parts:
C1, C2, C3, C4, C5, C6: 100nF/10%/X7R; C0603
C7: EEEFK1J220P; CAPAE800X650N
IC1, IC2: ATMEGA16A-PU; DIP1556W56P254L5232H483Q40N
J1: FTSH-105-01-L-DV-K-A-P-TR; FTSH10501LDVKAPTR
J4: PJ-031DH; PJ031DH
JP2: PINHD-1X2; 1X02
R1, R2, R3, R4: 10K/10%; R0603
S1, S2: PTS647SM50SMTR2LFS

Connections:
+5V/1: C1.1, C2.1, C3.1, C4.1, C5.1, C6.1, C7.1 (+), IC1.10 (VCC), IC1.30 (AVCC), IC1.32 (AREF), IC2.10 (VCC), IC2.30 (AVCC), IC2.32 (AREF), J1.7, J4.1 (SLEEVE), R1.2, R2.2, R3.2, R4.2; also elsewhere on the board
GND: C1.2, C2.2, C3.2, C4.2, C5.2, C6.2, C7.2 (-), IC1.11 (GND), IC1.31 (GND_1), IC2.11 (GND), IC2.31 (GND_1), J1.6, J1.10, J4.2 (TIP), JP2.1, S1.3, S1.4, S2.3, S2.4; also elsewhere on the board
HALL_DIR-LOWER: IC2.16 ([INT0]_PD2); also elsewhere on the board
HALL_DIR-UPPER: IC2.17 ([INT1]_PD3); also elsewhere on the board
HALL_SPEED-LOWER: IC2.15 ([TXD]_PD1); also elsewhere on the board
HALL_SPEED-UPPER: IC2.14 ([RXD]_PD0); also elsewhere on the board
LCD-DB0: IC1.40 (PA0_[ADC0]); also elsewhere on the board
LCD-DB1: IC1.39 (PA1_[ADC1]); also elsewhere on the board
LCD-DB2: IC1.38 (PA2_[ADC2]); also elsewhere on the board
LCD-DB3: IC1.37 (PA3_[ADC3]); also elsewhere on the board
LCD-DB4: IC1.36 (PA4_[ADC4]); also elsewhere on the board
LCD-DB5: IC1.35 (PA5_[ADC5]); also elsewhere on the board
LCD-DB6: IC1.34 (PA6_[ADC6]); also elsewhere on the board
LCD-DB7: IC1.33 (PA7_[ADC7]); also elsewhere on the board
LCD-E: IC1.3 ([INT2/AIN0]_PB2); also elsewhere on the board
LCD-R/W: IC1.2 ([T1]_PB1); also elsewhere on the board
LCD-RS: IC1.1 ([XCK/T0]_PB0); also elsewhere on the board
MOTOR_OVER-CURRENT: IC2.40 (PA0_[ADC0]); also elsewhere on the board
unnamed: IC2.2 ([T1]_PB1), JP2.2
RGB-INT: IC1.16 ([INT0]_PD2); also elsewhere on the board
RGB-LED: IC1.18 ([OC1B]_PD4); also elsewhere on the board
RST: IC1.9 (!RESET), IC2.9 (!RESET), J1.8, R1.1, R4.1, S1.1, S1.2, S2.1, S2.2
SCL: IC1.22 (PC0_[SCL]), IC2.22 (PC0_[SCL]), R3.1; also elsewhere on the board
SDA: IC1.23 (PC1_[SDA]), IC2.23 (PC1_[SDA]), R2.1; also elsewhere on the board
SERVO-LOWER: IC2.19 ([OC1A]_PD5); also elsewhere on the board
SERVO-UPPER: IC2.18 ([OC1B]_PD4); also elsewhere on the board
TCK: IC1.24 (PC2_[TCK]), IC2.24 (PC2_[TCK]), J1.1
TDI: IC1.27 (PC5_[TDI]), IC2.27 (PC5_[TDI]), J1.5
TDO: IC1.26 (PC4_[TDO]), IC2.26 (PC4_[TDO]), J1.2
TMS: IC1.25 (PC3_[TMS]), IC2.25 (PC3_[TMS]), J1.3
TRST: J1.9

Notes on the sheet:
JaG HetER BoB
Programming header
µC#1 (Master device)
µC#2 (Motor controller)
DC input jack
Decoupling capacitors

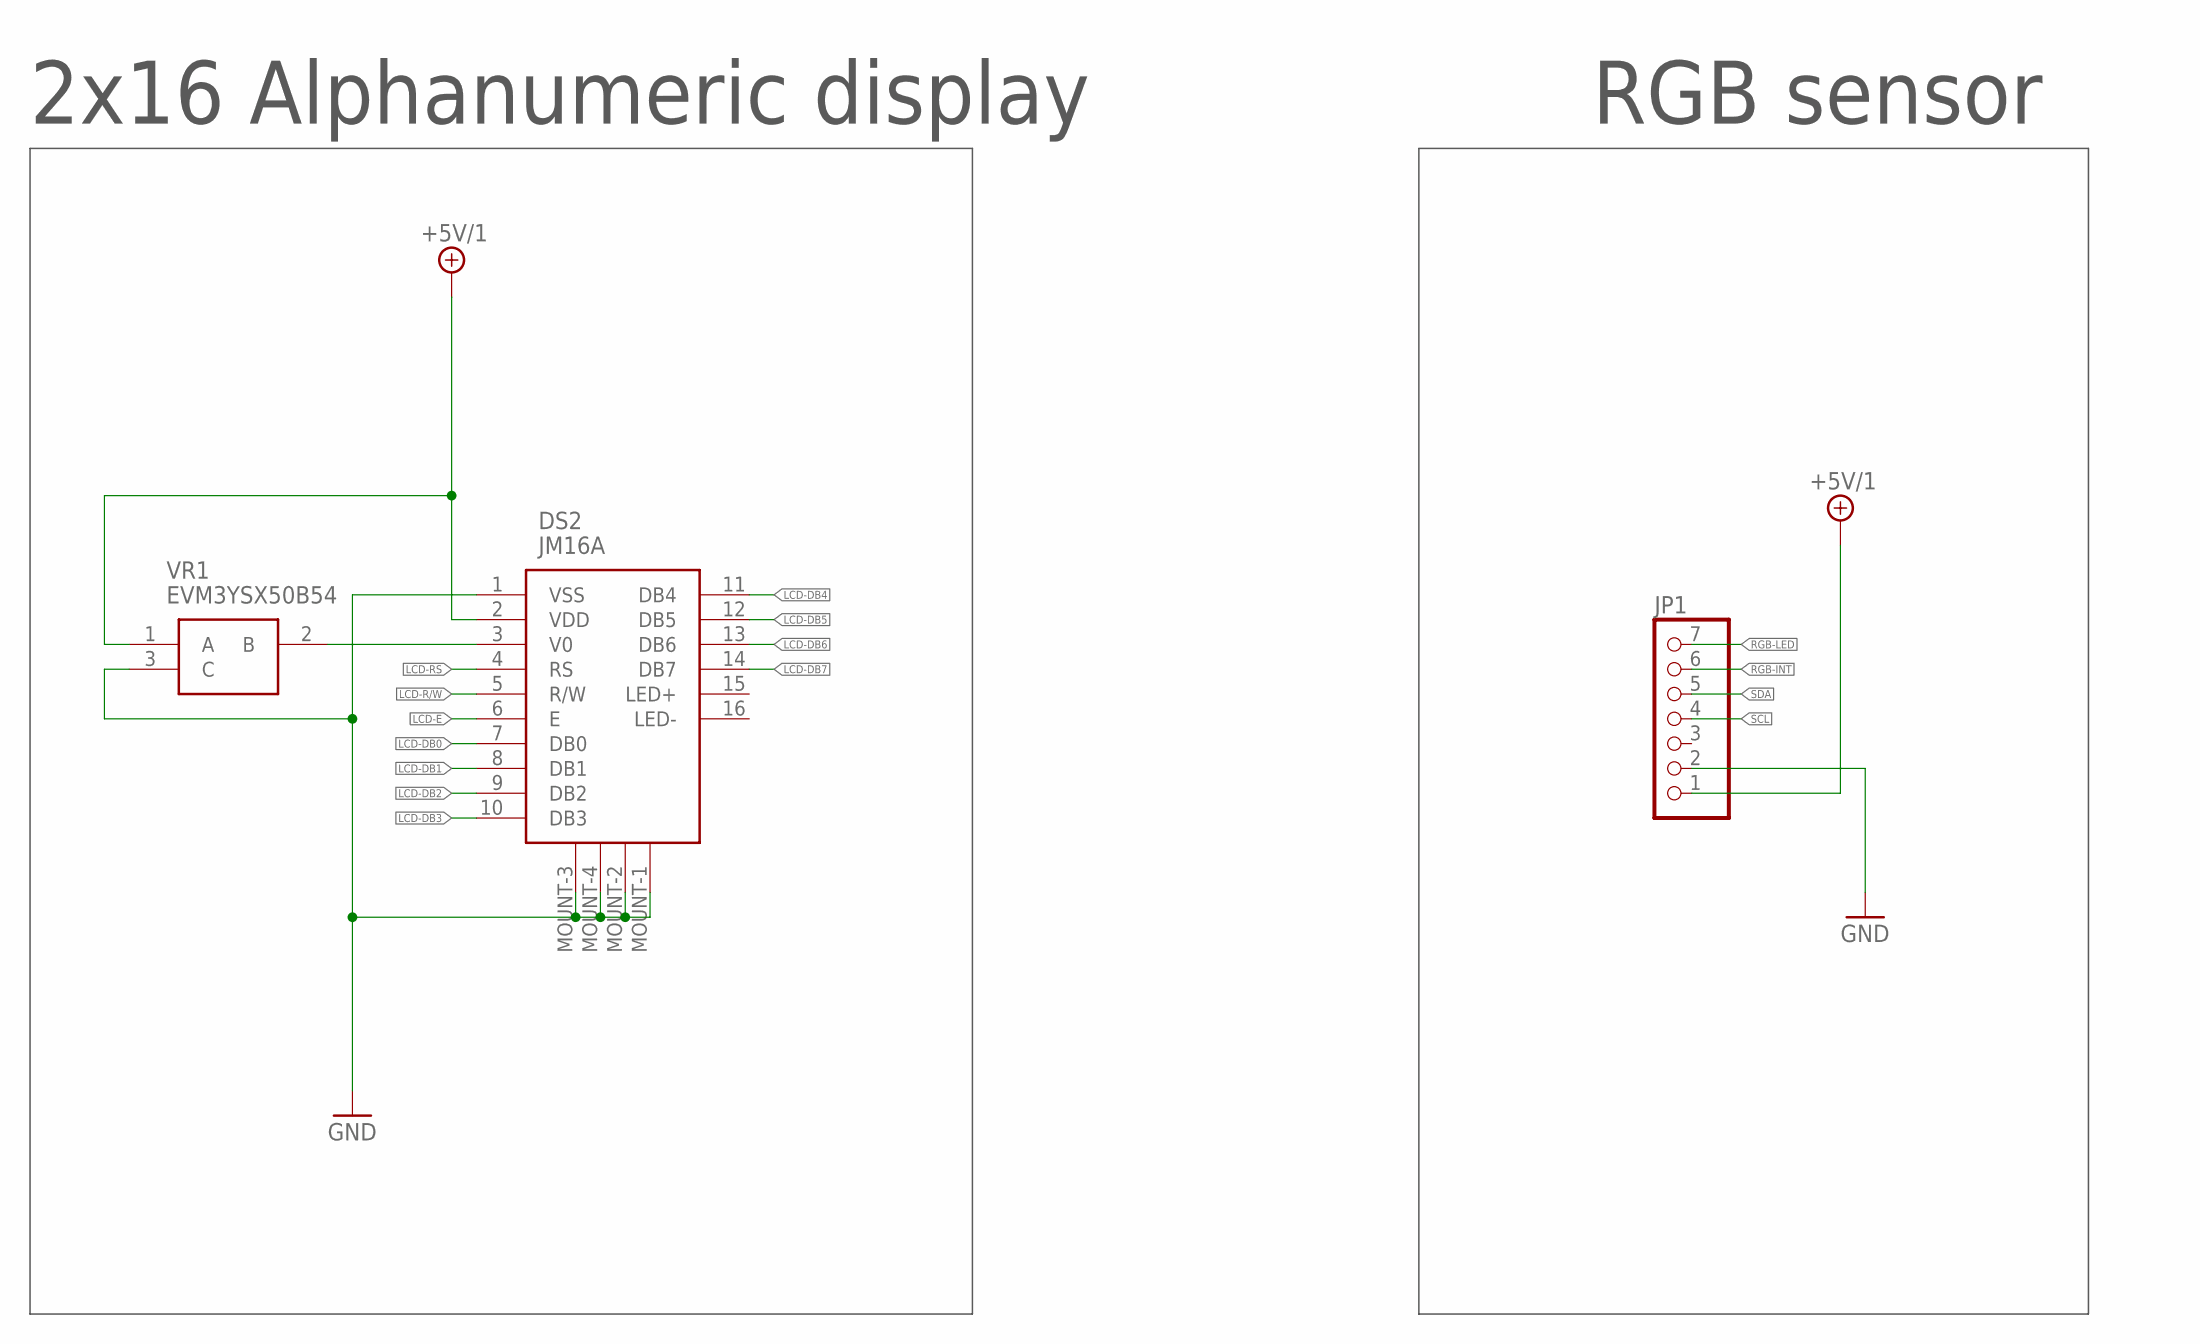
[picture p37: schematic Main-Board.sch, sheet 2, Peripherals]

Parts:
DS2: JM16A
JP1: PINHD-1X7; 1X07
VR1: EVM3YSX50B54

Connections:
+5V/1: DS2.2 (VDD), JP1.1, VR1.1 (A); also elsewhere on the board
GND: DS2.1 (VSS), DS2.MOUNT-1 (MOUNT-4), DS2.MOUNT-2 (MOUNT-3), DS2.MOUNT-3 (MOUNT-1), DS2.MOUNT-4 (MOUNT-2), JP1.2, VR1.3 (C); also elsewhere on the board
LCD-DB0: DS2.7 (DB0); also elsewhere on the board
LCD-DB1: DS2.8 (DB1); also elsewhere on the board
LCD-DB2: DS2.9 (DB2); also elsewhere on the board
LCD-DB3: DS2.10 (DB3); also elsewhere on the board
LCD-DB4: DS2.11 (DB4); also elsewhere on the board
LCD-DB5: DS2.12 (DB5); also elsewhere on the board
LCD-DB6: DS2.13 (DB6); also elsewhere on the board
LCD-DB7: DS2.14 (DB7); also elsewhere on the board
LCD-E: DS2.6 (E); also elsewhere on the board
LCD-R/W: DS2.5 (R/W); also elsewhere on the board
LCD-RS: DS2.4 (RS); also elsewhere on the board
unnamed: DS2.3 (V0), VR1.2 (B)
RGB-INT: JP1.6; also elsewhere on the board
RGB-LED: JP1.7; also elsewhere on the board
SCL: JP1.4; also elsewhere on the board
SDA: JP1.5; also elsewhere on the board

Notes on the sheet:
2x16 Alphanumeric display
RGB sensor

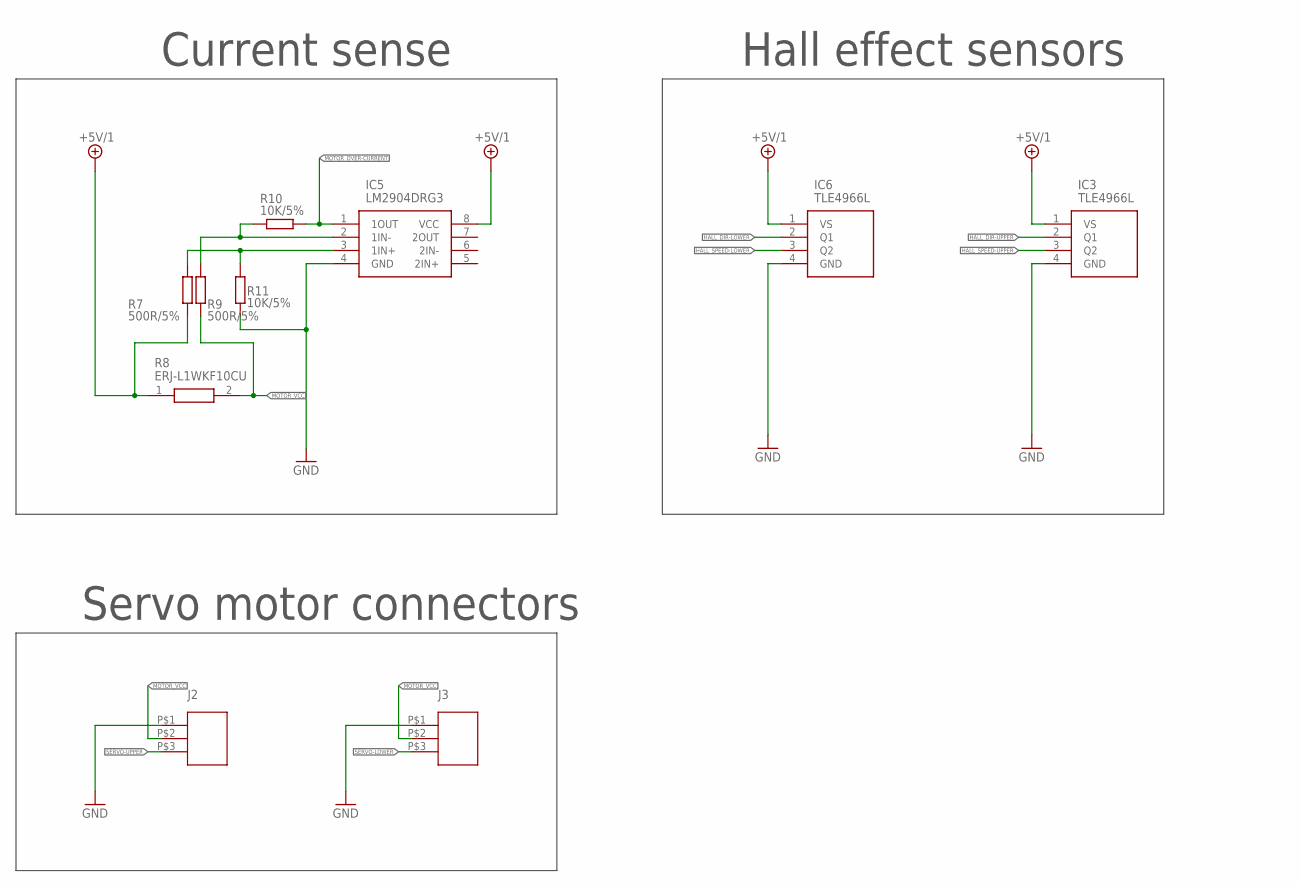
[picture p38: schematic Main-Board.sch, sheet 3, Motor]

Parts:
IC3, IC6: TLE4966L
IC5: LM2904DRG3; SOIC127P600X175-8N
J2, J3: 0022288033
R7, R9: 500R/5%; R0603
R8: ERJ-L1WKF10CU; RESC6332X120N
R10, R11: 10K/5%; R0603

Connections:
+5V/1: IC3.1 (VS), IC5.8 (VCC), IC6.1 (VS), R7.1, R8.1 (R1); also elsewhere on the board
GND: IC3.4 (GND), IC5.4 (GND), IC6.4 (GND), J2.P$1 (1), J3.P$1 (1), R11.1; also elsewhere on the board
HALL_DIR-LOWER: IC6.2 (Q1); also elsewhere on the board
HALL_DIR-UPPER: IC3.2 (Q1); also elsewhere on the board
HALL_SPEED-LOWER: IC6.3 (Q2); also elsewhere on the board
HALL_SPEED-UPPER: IC3.3 (Q2); also elsewhere on the board
MOTOR_OVER-CURRENT: IC5.1 (1OUT), R10.2; also elsewhere on the board
MOTOR_VCC: J2.P$2 (2), J3.P$2 (2), R8.2 (R2), R9.1
unnamed: IC5.3 (1IN+), R7.2, R11.2
unnamed: IC5.2 (1IN-), R9.2, R10.1
SERVO-LOWER: J3.P$3 (3); also elsewhere on the board
SERVO-UPPER: J2.P$3 (3); also elsewhere on the board

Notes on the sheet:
Current sense
Hall effect sensors
Servo motor connectors

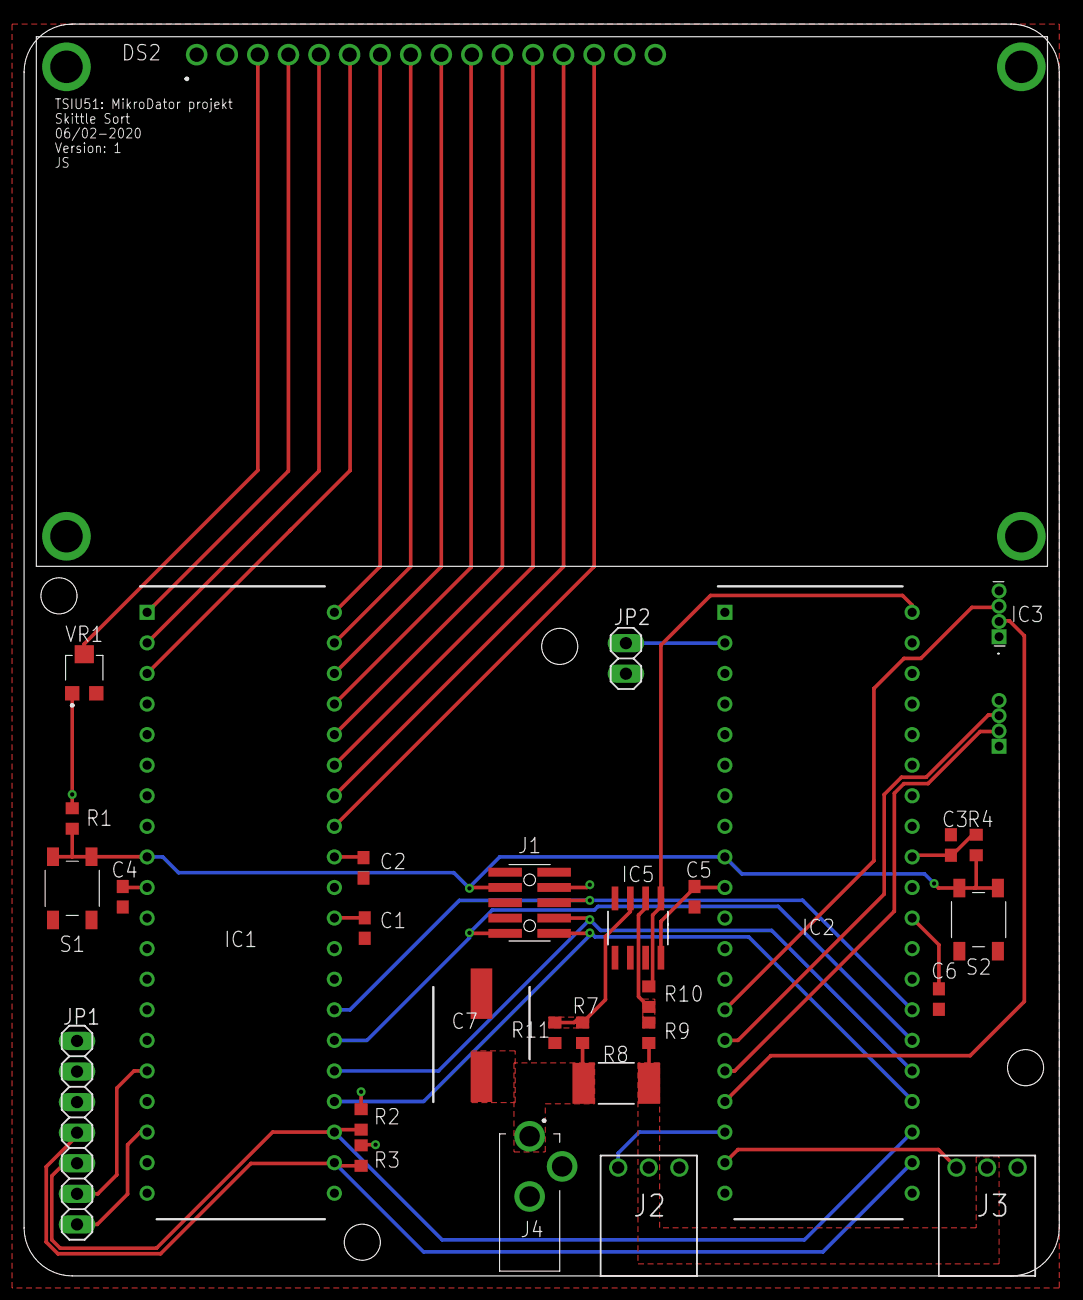
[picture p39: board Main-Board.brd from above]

Board: 2 copper layers, 86.0 x 104.0 mm, 31 parts (1 on the bottom side), 34 nets.

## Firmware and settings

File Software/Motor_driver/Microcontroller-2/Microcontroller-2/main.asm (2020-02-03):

;motor processor






	.cseg
	.org	0
	jmp		START
	.org	INT0addr
	jmp		UPPER_TRIGGER
	.org	INT1addr
	jmp		LOWER_TRIGGER
	.org	OVF1addr
	jmp		SERVO_DIRECTION



	.dseg
	.org	SRAM_START
POSU:
	.byte	1	;Upper slab possission
POSL:
	.byte	1	;Lower slab possission
COLOR_POS:
	.byte	1	;current color possission
	.cseg


	.equ	SERVO_RR	= 2600		;Refresh rate
	.equ	SERVO_CW	= 300		;Clockwise
	.equ	SERVO_CCW	= 0			;Counter clockwise
	.equ	SERVO_ST	= 0			;Stop


	;---code
START:
	ldi		r16, HIGH(RAMEND)
	out		SPH, r16
	ldi		r16, LOW(RAMEND)
	out		SPL, r16
	;
    call	HW_INIT
	;


	ldi		r16, HIGH(SERVO_CW)
	out		OCR1BH, r16
	ldi		r16, LOW(SERVO_CW)
	out		OCR1BL, r16
LOOP:
    rjmp	LOOP
;---------------------------------------


;***Eatch time the the drum passes a color dump***
UPPER_TRIGGER:
	;push all used
	push	r16
	in		r16, SREG
	push	r16
	;

	;pull all used
	pop		r16
	out		SREG, r16
	pop		r16
	reti
;----------------------------------------




;***Eatch time the the drum passes a color dump***
LOWER_TRIGGER:
	;push all used
	push	r16
	in		r16, SREG
	push	r16
	push	r17
	;
	in		r16, PINB	
	cpi		r16, 0		;clockwise if 1
	breq	CCW_DIR
CW_DIR:
	lds		r16, (POSL)
	inc		r16
	rjmp	DIR_LIM
CCW_DIR:
	lds		r16, (POSL)
	dec		r16
	;
DIR_LIM:
	ori		r16, 0	;check negative
	brmi	UND_LIM	;under limit
	cpi		r16, 5	;over limit
	brne	POS_OK
	subi	r16, 1	;***utanför sensor***
UND_LIM:
	inc		r16		;***utanför sensor***
	;
POS_OK:
	sts		(POSL), r16	;new pos
	lds		r17, (COLOR_POS)
	cp		r16, r17
	brne	NO_DROP
DROP:
	ldi		r16, HIGH(SERVO_ST)
	out		OCR1BH, r16
	ldi		r16, LOW(SERVO_ST)
	out		OCR1BL, r16
NO_DROP:
	;pull all used
	pop		r17
	pop		r16
	out		SREG, r16
	pop		r16
	reti
;----------------------------------------


SERVO_DIRECTION:
	;push all used
	push	r16
	in		r16, SREG
	push	r16
	;		

	;pull all used
	pop		r16
	out		SREG, r16
	pop		r16
	reti
;----------------------------------------






HW_INIT:
	;interupt for drum trigger
	ldi		r16, (1<<ISC00)|(1<<ISC01)|(1<<ISC11)|(1<<ISC10)
	out		MCUCR, r16
	ldi		r16, (1<<INT0)|(1<<INT1)
	out		GICR, r16

	ldi		r16, 0xF0	
	out		DDRD, r16	;D 4-7 output

	ldi		r16, 0x00
	out		DDRB, r16	;B input 

TIMER_INIT:
	; Setting counter mode 
	ldi		r16, (1<<WGM13)|(1<<WGM12)
	out		TCCR1B, r16

	ldi		r16, (1<<WGM11)|(0<<WGM10)|(1<<COM1A1)|(0<<COM1A0)|(1<<COM1B1)|(0<<COM1B0)
	out		TCCR1A, r16

	; Setting max counter value before overflow
	ldi		r16, HIGH(SERVO_RR)
	out		ICR1H, r16
	ldi		r16, LOW(SERVO_RR)
	out		ICR1L, r16

	; Setting prescaling and interrupt
	in		r16, TCCR1B  
	ori		r16,(0<<CS12)|(1<<CS11)|(1<<CS10) ;Prescaler set to F_CPU/64 (S:108)

	out		TCCR1B, r16
	ldi		r16, 1<<TOIE1
	out		TIMSK, r16
	sei
	ret

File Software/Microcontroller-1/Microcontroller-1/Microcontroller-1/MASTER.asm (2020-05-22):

//////// TSIU51 SKITTLE SORT ////////////////////////////////////////////////
//////// ATMEGA16A CONFIG ///////////////////////////////////////////////////
//CPU CLOCK 8 MHz
//BOOT FUSE 64 ms
//////// RBG_SENSOR STATIC REGISTERS ////////////////////////////////////////
.equ RGB_ENABLE =0x00
.equ RGB_ATIME = 0x01
.equ RGB_WTIME = 0x03
.equ RGB_AILTL = 0x04
.equ RGB_AILTH = 0x05
.equ RGB_AIHTL = 0x06
.equ RGB_AIHTH = 0x07
.equ RGB_PERS  = 0x0C
.equ RGB_CONFIG = 0x0D
.equ RGB_CONTROL = 0x0F
.equ RGB_ID = 0x12
.equ RGB_STATUS = 0x13
.equ RGB_CDATAL = 0x14
.equ RGB_CDATAH = 0x15
.equ RGB_RDATAL = 0x16
.equ RGB_RDATAH = 0x17
.equ RGB_GDATAL = 0x18
.equ RGB_GDATAH = 0x19
.equ RGB_BDATAL = 0x1A
.equ RGB_BDATAH = 0x1B

.equ RGB_COMMAND_BIT = 0x80
.equ RGB_AUTO_INC_BIT = 0b00100000
//////// RGB-SENSOR USER CONFIG ////////////////////////////////////////
.equ ATIME_VALUE = 0xD0 // NUMBER OF INTEGRATION CYCLES = 256-ATIME_VALUE (0xFF+1 -ATIME_VALUE) WITH EACH CYCLE TAKING 2.5 ms 
.equ GAIN_VALUE  = 0x00 //00=1X, 01=4X, 10=16X, 11=60X
//////// COLOR COMPARE CONFIG /////////////////////////////////////////
.equ PRECISION   = 64  //SCALES UP OUR REFERENCE-CLEARVALUES FOR MATH REASONS. CLEARDATA*PRECISION SHOULD BE AS CLOSE TO 16 BIT WITHOUT OVERFLOWING
.equ PRECISION_EXP = 6  // EXPONENT OF PRECISION IN BASE 2
.equ CLEAR_DIFF_DIV = 8  // SCALES DOWN OUR CLEAR-DIFFERENCE BY THIS NUMBER TO GIVE IT LESS INFLUENCE ON OVERALL DIFFERENCE
.equ CLEAR_DIFF_DIV_EXP = 3 // EXPONENT OF CLEAR_DIFF_DIV IN BASE 2
//////// COLOR ALIAS //////////////////////////////////////////////////
.equ NUMBER_OF_COLORS = 6 //5 or 6, depends on if we want NO_SKITTLE
.equ RED_SKITTLE    = 0
.equ GREEN_SKITTLE  = 1
.equ ORANGE_SKITTLE = 2
.equ YELLOW_SKITTLE = 3
.equ PURPLE_SKITTLE = 4
.equ NO_SKITTLE     = 5
//////// TWI USER CONFIG ////////////////////////////////////////////////
.equ TWI_BITRATE   = 32  //100kHz
.equ TWI_PRESCALAR = 0 //100kHz
//////// TWI SLAVE ADDR /////////////////////////////////////////////////
.equ RGB_SLAVE_ADDR = 0x29
.equ MCU_SLAVE_ADDR = 0x69
//////// TWI TWSR HANDLING CODES ////////////////////////////////////////	
.equ TWSR_TWI_START = 0x08
.equ TWSR_TWI_REP_START		= 0x10
.equ TWSR_MT_SLA_ACK		= 0x18
.equ TWSR_MT_SLA_NACK		= 0x20 //PROBLEM
.equ TWSR_MT_DATA_ACK		= 0x28
.equ TWSR_MT_DATA_NACK		= 0x30 //PROBLEM
.equ TWSR_ARBITRATION_LOST	= 0x38 //PROBLEM

.equ TWSR_MR_SLA_ACK		= 0x40
.equ TWSR_MR_SLA_NACK		= 0x48 //PROBLEM
.equ TWSR_MR_DATA_ACK		= 0x50
.equ TWSR_MR_DATA_NACK		= 0x58
//////// LCD CONSTANTS /////////////////////////////////////////////////
.equ RS = 0
.equ RW = 1
.equ E = 2
.equ Clear_Display = 0b00000001
.equ Return_Home   = 0b00000010
.equ Second_Line_Address = 0b11000000
//////// SKITTLE REFERENCE VALUES /////////////////////////////////////
// ALL CLEAR-VALUE*PRECISION MUST BE WITHIN 16bit
// REFERENCE VALUES MEASURED WITH: GAIN_VALUE = 0x00, ATIME_VALUE = 0xD0
//RED:
	.equ RED_CLEAR = 679
	.equ RED_RED = 232
	.equ RED_GREEN = 222
	.equ RED_BLUE = 200

//GREEN:
	.equ GREEN_CLEAR = 708
	.equ GREEN_RED = 226
	.equ GREEN_GREEN = 248
	.equ GREEN_BLUE = 211

//ORANGE:
	.equ ORANGE_CLEAR = 733
	.equ ORANGE_RED = 261
	.equ ORANGE_GREEN = 239
	.equ ORANGE_BLUE = 211

//YELLOW:
	.equ YELLOW_CLEAR = 763
	.equ YELLOW_RED = 267
	.equ YELLOW_GREEN = 261
	.equ YELLOW_BLUE = 217

//PURPLE:
	.equ PURPLE_CLEAR = 674
	.equ PURPLE_RED = 218
	.equ PURPLE_GREEN = 226
	.equ PURPLE_BLUE = 205

//NO_SKITTLE:
	.equ NO_SKITTLE_CLEAR = 651
	.equ NO_SKITTLE_RED = 208
	.equ NO_SKITTLE_GREEN = 220
	.equ NO_SKITTLE_BLUE = 198
//////// MEMORY LAYOUT //////////////////////////////////////////////
	.dseg
	.org 0x0060 //SRAM_START
//////// LATEST CRGB-VALUES /////////////////////////////////////////
CDATAL:	.byte 1
CDATAH:	.byte 1
RDATAL:	.byte 1
RDATAH:	.byte 1
GDATAL:	.byte 1
GDATAH:	.byte 1
BDATAL:	.byte 1
BDATAH:	.byte 1

//////// LATEST SKITTLE DIFFERENCES ///////////////////////////////////
RED_SKITTLE_DIFF:
	.byte 2
GREEN_SKITTLE_DIFF:
	.byte 2
ORANGE_SKITTLE_DIFF:
	.byte 2
YELLOW_SKITTLE_DIFF:
	.byte 2
PURPLE_SKITTLE_DIFF:
	.byte 2
NO_SKITTLE_DIFF:
	.byte 2
//////// COLOR OF LATEST SKITTLE SORTED ///////////////////////////////////
// 0 = RED, 1 = GREEN, 2 = ORANGE, 3 = YELLOW, 4 = PURPLE, 5 = NO_SKITTLE
LATEST_SKITTLE_COLOR:
	.byte 1
//////// NUMBER OF SKITTLES SORTED ////////////////////////////////////////
RED_N:
	.byte 1
GREEN_N:
	.byte 1
ORANGE_N:
	.byte 1
YELLOW_N:
	.byte 1
PURPLE_N:
	.byte 1
NO_SKITTLE_N:
	.byte 1
//////// CURRENT TWI SLAVE //////////////////////////////////////////////
CURRENT_SLAVE:
	.byte 1
	.cseg
//END OF MEMORY LAYOUT
//////// RESET/INTERRUPT VECTORS ////////////////////////////////////////
.org 0
	jmp	BOOT
.org INT0ADDR
	jmp	ISR_INT0	
/////////////////////////////////////////////////////////////////////////
.org 0x02A
BOOT://FUSE IS SET TO 64 ms STARTUP 

	ldi	r16, HIGH(RAMEND)
	out	SPH, r16
	ldi	r16, LOW(RAMEND)
	out	SPL, r16

	ldi	YH,HIGH(SRAM_START)
	ldi	YL,LOW(SRAM_START) 
	ldi	r16, 28 //NUMBER OF BYTES IN SRAM
	call	INIT_CLEAR_SRAM // CLEAR N BYTES FROM Y POINTER
	call	INT0_INIT
	call	TWI_INIT
	call	LCD_INIT
	call	RGB_INIT
	call	UPDATE_DISPLAY
	sei 
	jmp MAIN

///////////////////////////////////////////////////////////////////

MAIN:	
	rjmp	MAIN
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

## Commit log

2020-01-23 Initial funnel commit
    [Funnel.SLDPRT]
2020-01-23 Initiation of PCB project files
    [Main-Board.brd, Main-Board.sch]
2020-01-25 Added an alternative spec and flow chart
2020-01-25 Updated teh funnel to support teh size of the skittles, also added a skittle
    [Funnel.SLDPRT, Skittle.SLDPRT]
2020-01-25 Added upper disk
    [Upper-Disk.SLDPRT]
2020-01-25 Added lower disk and removed temp file
    [Lower-Disk.SLDPRT]
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2020-01-25 Added temporary motor and updated Lower Disk
    [Lower-Disk.SLDPRT, Parallax-900-000XX_ServoMotor.SLDPRT]
2020-01-25 Added proof of concept slide
    [Slide.SLDPRT]
2020-01-25 Första försök till LCD-drivers
    Enbart kollat i databladen och föreläsnings-pdf och utgått ifrån det. Kompilerad i simulatorn
2020-01-25 Added Manufacturers CAD-Files
    [User Library-Futaba-Parallax-ContinuousRatationServo.sldprt, User Library-Futaba-Servo-X-Horn.sldprt]
2020-01-25 Updated mechanical components
    [Skittle-Sort-Assembly.SLDASM, Slide.SLDPRT, Top-Sorter-SubAssembly.SLDASM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]
2020-01-25 Updated assembly
    [2mm-Screw.SLDPRT, Top-Holder.SLDPRT, Top-Motor-Holder.SLDPRT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]
2020-01-27 Börja på motor processor
2020-01-27 Updated shape
    [Lower-Disk.SLDPRT, User Library-Futaba-Servo-X-Horn.sldprt]
2020-01-27 Updates and refined mechanical components
    [Funnel.SLDPRT, Skittle-Sort-Assembly.SLDASM, Slide.SLDPRT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]
2020-01-28 Börja på motor microkontroll
2020-01-28 Updated schematic and ignore all backup files
    [Main-Board.brd, Main-Board.sch]
2020-01-28 Updated schematic
    [Main-Board.brd, Main-Board.sch]
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2020-01-28 Updated schematic
    Added a similar LCD and µC:2
    [Main-Board.brd, Main-Board.sch]
2020-01-28 Added motor things to schematic
    [Main-Board.brd, Main-Board.sch]
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2020-01-28 Did some layout
    [Main-Board.brd, Main-Board.sch]
2020-01-29 Updated layout
    [Main-Board.brd, Main-Board.sch]
2020-01-29 Prelimenary layout
    [Main-Board.brd]
2020-01-29 Updated mechanical parts
    [Lower-Disk.SLDPRT, Skittle-Sort-Assembly.SLDASM, Slide.SLDPRT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]
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2020-01-30 Updated schematci for more componenets
    [Main-Board.brd, Main-Board.sch]
2020-01-30 Added temp BOM from EAGLE
    [Main-Board.xlsx]
2020-01-30 Create Motor lite bättre
2020-02-01 Updated mechanical files, with a semi new solution
    [BOM.xlsx, Lower-Disk.SLDPRT, M3x16mm.SLDPRT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]
2020-02-01 Only need to add funnel
    [Skittle-Sort-Assembly.SLDASM, Slide.SLDPRT, Upper-Disk-ALT.SLDPRT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]
2020-02-03 la till på interupten
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2020-02-05 Added the final components to the schmatic and updated the layout
    [Main-Board.brd, Main-Board.sch, Main-Board.xlsx]
2020-02-06 LCD is wrong, need to finish teh new footprint for it.
    [Main-Board.brd, Main-Board.sch]
2020-02-06 Updated display footprint and fixed layout to suit it.
    [Main-Board.brd, Main-Board.sch]
2020-02-06 Final PCB. Added GERBER files for MF
    [BOM.xlsx, Main-Board.brd, Main-Board.sch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]
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2020-02-10 Enlarged servo motor mount
    [Upper-Servo-Gear.SLDPRT]
2020-02-10 Made some changes to the contruction
    [Lower-Disk.SLDPRT, Shaft-Spacer.SLDPRT, Skittle-Sort-Assembly.SLDASM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]
2020-02-14 Fixed push overflow, works!
    [main.asm]
2020-02-20 Added bottom slide part
    Going to split it to make it easier to print
    [Slide-Bottom.SLDPRT]
2020-02-20 Updated bottom slide model and added STL file
    [Slide-Bottom.SLDPRT, Slide-Bottom.STL]
2020-02-23 Updated slide assembly, added a color for the shaft, added RGB sensor and added magnet placement/ hall sensor
    [Lower-Disk.SLDPRT, Skittle-Sort-Assembly.SLDASM, Slide-BACKUP.SLDPRT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]
2020-02-23 Lagt till Push/pop, Wait-funktion. Utveckla denna!
    Lagt till modulär Wait-funktion som beror på Atime. Mer konstanter och config uppe i början av programmet. RGB_INIT, RGB_SHUTDOWN och börjat så smått på ERROR_HANDLING på TWI.
    [I2CRGB.asm]
2020-02-24 Added STL files
    [Lower-Disk.STL, Upper-Shaft-Retainer.STL]
2020-02-24 Ger logiska värden! NICE!!!
    ATIME måste vara 0x00!!! READ6REGISTERS verkade funka när vi fixade ett fel!
    [I2CRGB.asm]
2020-02-24 Updated model and added mounting points for RGB sensor and the hall effect sensor
    [Lower-Disk.SLDPRT, Magnet-8mm.SLDPRT, Skittle-Sort-Assembly.SLDASM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]
2020-03-03 Enlarged hole for RGB sensor
    [Skittle-Sort-Assembly.SLDASM, Upper-Disk-ALT.SLDPRT]
2020-03-04 Main_nr2
    hela microcontroller 2 med många problem med magneter
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2020-03-06 Updated Slide-Top to mount a funnel to it
    [2mm-Screw.SLDPRT, Funnel.SLDPRT, Lower-Disk.SLDPRT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]
2020-03-08 Added images and updated model for exploded view, also added it to the prsentation
    [Skittle-Sort-Assembly.SLDASM]
2020-03-09 Added images andupdated presentation
    [Disk-Draw.SLDDRW, Skittle-Sort-Assembly.SLDASM]
2020-03-10 Sorterar och sånt
    Fixat off-by-one vid start!
    Lagt till Vilket håll den ska snurra i I2C interupten
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2020-03-10 Added funnel rtaiuner and updated funnel
    Also added some renderings to the image collection
    [Floor.SLDPRT, Funnel Retainer.SLDPRT, Funnel.SLDPRT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]
2020-03-11 Added stl file
    [Funnel Retainer.STL, Funnel.STL]
2020-03-11 Added Cup STL
    [Cup.STL]
2020-03-12 Utökat Difference i SRAM till 16bit
    Nästa steg är att skapa weights för de olika Differences?
2020-03-13 Lagt till TWI ERROR HANDLER
    Skriver ut på LCD om nån TWI gick åt helvete. Nya mätvärden utan tratt och funkar okej. Med tratt blir allt Purple.
    [RGBAndLCDWithFilter.asm]
2020-03-13 Sänkt hastighet på CCW. GÖRA OLIKA HASTIGHETER FÖR ÖVRE/UNDRE?
    Fick ändra stop-värdet då den drifta lite. Sänkte hastigheten rejält på övre trumman så den stannar exaktare framför sensorn.
2020-03-15 Räknar med Clear Diff. Kan se Mätdata på LCD, NY BCD till LCD-funktion
    Räknar ut clear diff och dividerar ner till valfri multipel av 2. Därför är Clearvärdena inte längre uppskalade i Lookup-tablen. Skalas upp i Normalize_Data istället. Får se om detta hjälper.
    Har även lagt till funktion som skriver CRGBDATA (rådata) till skärmen så vi kan debugga. Fick då skriva en ny funktion som printar 3 siffror till skärmen får det ska funka.
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2020-04-13 Added images
    [Skittle-Sort-Assembly.SLDASM]
2020-05-17 Uppdaterade några ritningar
    [2mm-Screw.SLDPRT, Floor.SLDPRT, Funnel Retainer.SLDPRT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]
